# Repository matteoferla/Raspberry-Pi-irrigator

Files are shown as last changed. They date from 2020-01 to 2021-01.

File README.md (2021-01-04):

# Raspberry-Pi-irrigator

> :skull: This project has been superceded by [https://github.com/matteoferla/Somewhat-Smart-Home](https://github.com/matteoferla/Somewhat-Smart-Home).

A Raspberry Pi controlled irrigation system to water plants based on soil moisture.
A pump waters the plant (a peter pepper chilli plant) based on its soil moisture, while the pi camera takes photos of it. 
—last year's attempt at gardening was an unmitigated disaster, so this year I am automating it.

[irrigator.matteoferla.com/](http://irrigator.matteoferla.com/)

This project is ongoing and these are my notes...

## Features

What the schematic looks like...

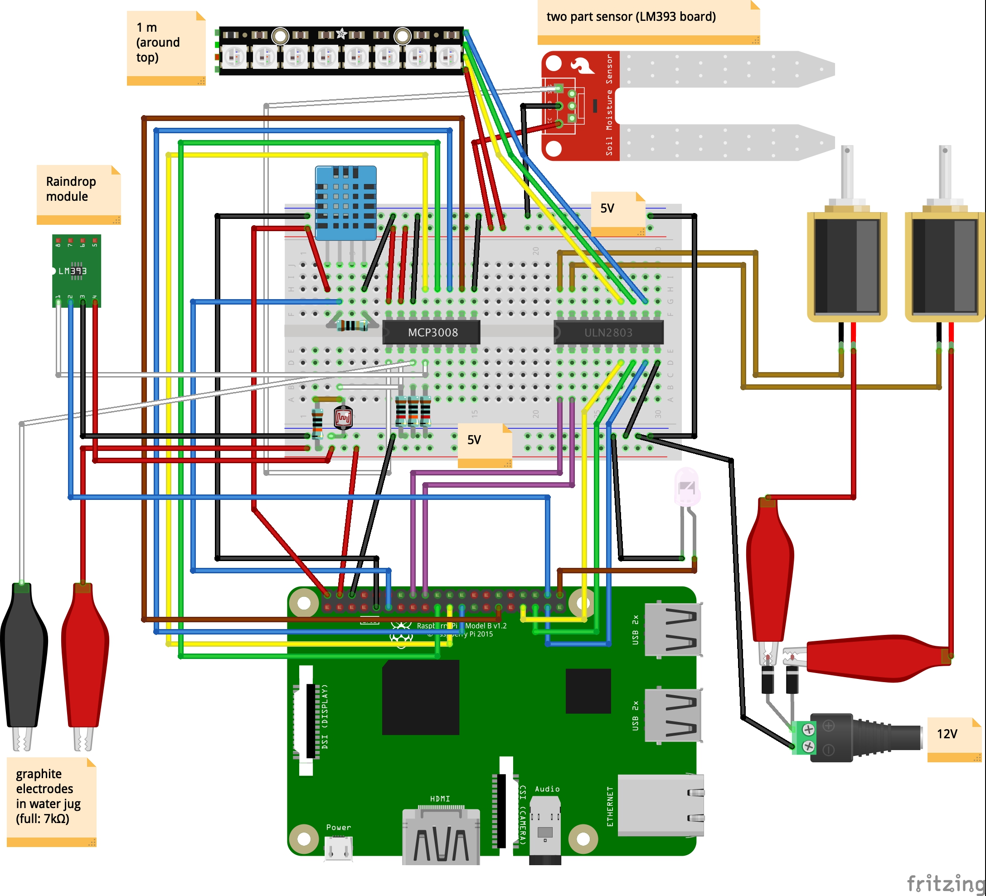
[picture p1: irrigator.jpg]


What it looks like in RL...



### Peter pepper plant

This bad boi is the key component. It's a peter pepper plant.

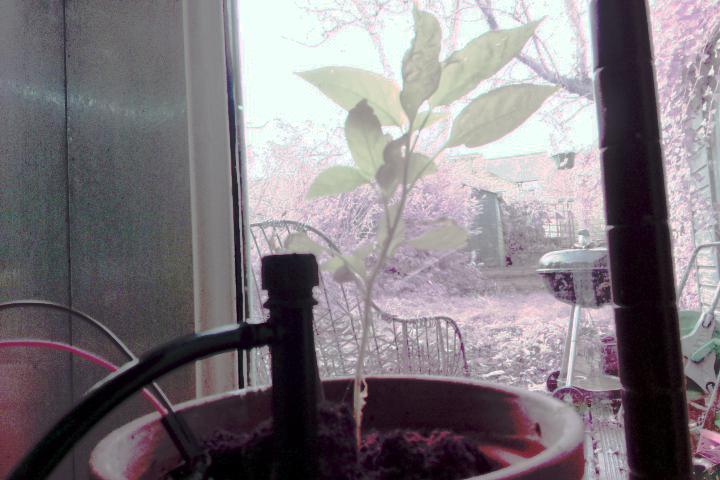
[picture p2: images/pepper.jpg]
pepper


### Pi

I am using a Pi 3+ with a MCP3008 chip and not an Arduino Uno*, because of the website business to check the status.

&lowast;)In my case, a fake Uno by Elegoo. 

I was going to use the Pi Zero but I want to use the camera (wich is for reg pi).

The downside is that my available Pi 3+ has a shorted 3.3V rail.
The reason for the short is that I placed another one the wrong way round —the AMS1117-3.3V voltage regulator on the power module blew a hole!
Maybe one day I will solder in a new PMIC. But for now I am using a externally powering the 5V and 3.3V rails via a breadboard power module MB102.
The GPIO pins and the 3.3V rail measure 2.2V without the external power, but seem fine with.
Powering a pi via the GPIO is bad as it may short the PMIC, due to current spikes.

I am not sure what the actual current is on the 5V and 3.3V rail.
The 12V supply is 2.5A and the module produces a max of 700mA. I'll assume it is that.



A problem with the power for the pi there is a USB and a 12V for the rail and a 12V for the motors and lights...



## pi Camera NoIR

My camera is the infrared camera for night mode.
So what about daytime? Maths to the rescue! (see [camera.md](camera.md))

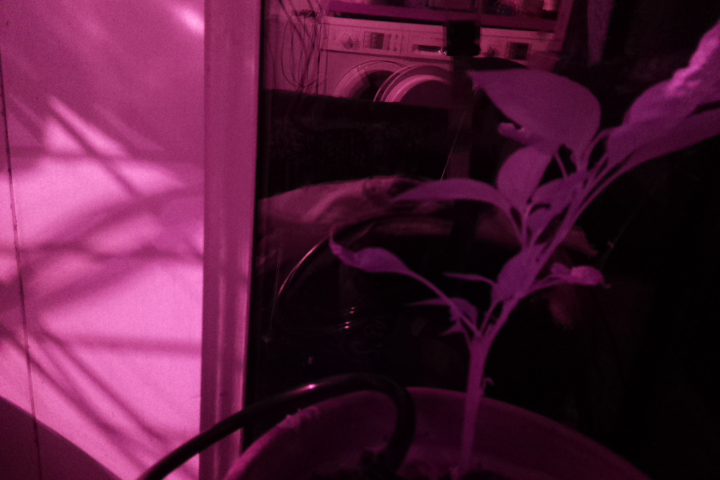
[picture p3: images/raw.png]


After histogram stretching and whitebalance correction in the YCbCr domain:

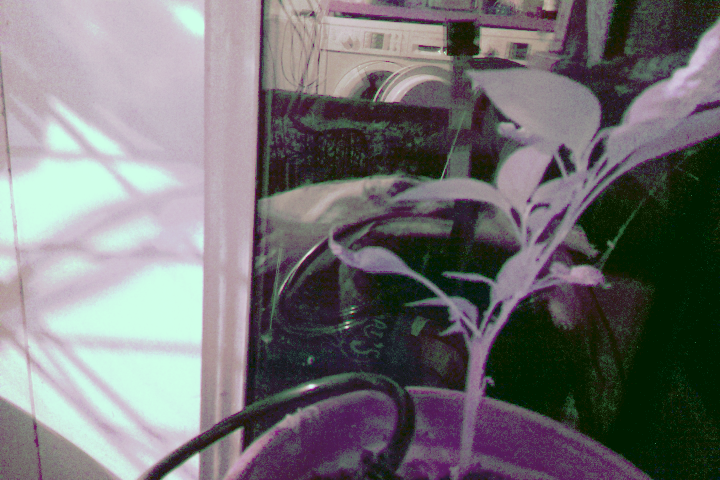
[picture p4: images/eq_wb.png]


For the nighttime, I am using a 1 meter LED strip.

## Photoresistor

Previously, I had the photoresistor in parallel going to ground.
However, this meant that it is was draining too power from the circuit during the day.
As a result, it is now in series with no pulldown.
Current does not flow through the analog in pins of the MCP3008 when it is not reading —hurray.
The GL5528 photoresistors are 10k&Omega; in the dark and 1M&Omega; in the light.
With a 1M&Omega; resistor beforehand in series, 
the output is 2.17V for 10k&Omega; (bright) and 1.7V for 1M&Omega; (dark).

### Formerly: Moisture via YL69
A resistance sensor (YL69 moisture sensor) measures the soil humidity every hour and if the soil resistance goes too low the pump is activated.

The arbitrary value of 50% threshold is based on plying with ramekins with soil. I baked some soil in the oven and then measured different levels of hydration.

I got ages back the YL69 moisture sensor from Kuman kit from Amazon. The YL-69 consists of an electrode and an amplifier (LM393) module. The YL69 oxidises over time (a month apparently).
So further down the line, I will need to switch the electrode to a pair of graphite leads or a capacitance sensor. LM393 is a comparator not a op-amp like a LM358.

Due to the amplifier it is always on.

As promised by the web it did get corroded.



### Moisture via capacitative sensor

I have the analog models. They have in the top part a `TLC555I LinCMOS Timer`, not an op amp or comparator like the others.
No idea what this does exactly.
It draws current even when the analog out is off.

Oddly, the two don't have matching values and aren't that great.

### Water level

The water in the jug is measured by two graphite electrodes. Aka. 2mm graphite cores for mechanical pencils from [Amazon](https://www.amazon.co.uk/gp/product/B0051OCJZ4/).
The jug is a credit card width (8 cm) and tap water has a resistance of 1 k&Omega; so that is 7k&Omega;, when full.
When empty it should be zero —see pulldown problem.



Oddly, the graphite rods had white lettering, which dissolved away leaving flakes.



In two weeks of submersion, the graphite seems fine.

## Pulldown resistors
Pull-down resistors make faint current go to zero. But they also close the circuit!
I put some in at first then took them out as they weren't doing much.

## Temperature

Whereas the DHT11 works fine with the circuitpython `adafruit_dht` library, DHT22 seems to work only with the older `adarfruit_DHT` one.
Here I am using a DHT22.

## Pumps

To water I need pumps and stuff:

* 2x Goso AB11 solenoid pumps [from eBay](https://www.ebay.co.uk/itm/12V-Dosing-Pump-Peristaltic-Head-For-Aquarium-Lab-Analytical-Water-Arduino-DIY/202050095537) in green and blue. The pumps run at 12V 7.5W. SO 7.5W÷12V=0.625A.
* STM ULN2803A Darlington Driver [from eBay](https://www.ebay.co.uk/itm/ULN2803A-Darlington-Driver-TRANSISTOR-ARRAY-8-NPN-x-2-pcs/222622920820). The darlington driver has inbuilt rectifier diodes. 
* AC/DC adaptor 12V⎓3A with standard ⊖-C*-⊕ coaxial and screw jack-thinggy adaptor.



Lessons learnt:

* So the pump out tube needs to be higher ground that the plant or else it flows back and drips.
* Tubing is expensive, but worth it! My cheap black tubing is horrendous: I should have gone for a pricier roll.
 
## Code

I am reusing chunks of code from my previous projects:

* [temp monitor site](https://github.com/matteoferla/Temperature-moniting-website-via-Rasberry-Pi)
* [Spirometry via photoresistor](https://github.com/matteoferla/Spirometry_via_photoresistor)

## Notes

* I connected the two gnds. Not sure if it's a good idea or not.
* Like always during construction I tested chunks of code on the Raspberry via a jupyter notebook it serves across the network (`jupyter notebook --ip="*"`).

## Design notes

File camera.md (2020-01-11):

This what the image looks like in low halogen bulb light 
raw

When I run

    with PiCamera() as camera:
        stream = BytesIO()
        camera.start_preview()
        time.sleep(5)
        camera.capture(stream, format='jpeg')
        stream.seek(0)
        im = Image.open(stream)
        display(im)

So first I apply histrogram stretching.
From [SO](https://stackoverflow.com/questions/7116113/normalize-histogram-brightness-and-contrast-of-a-set-of-images-using-python-im)
I copied the following, which acts on a image.

    def histogram_stretch(im: Image) -> Image:
        h = im.convert("L").histogram()
        lut = []
        for b in range(0, len(h), 256):
            # step size
            step = functools.reduce(operator.add, h[b:b + 256]) / 255
            # create equalization lookup table
            n = 0
            for i in range(256):
                lut.append(n / step)
                n = n + h[i + b]
        # map image through lookup table
        return im.point(lut * 3)
    
While from [here](https://opencv-python-tutroals.readthedocs.io/en/latest/py_tutorials/py_imgproc/py_histograms/py_histogram_equalization/py_histogram_equalization.html)
I made the following, which acts on numpy arrays.

    def histogram_stretch(t: np.ndarray) -> np.ndarray:
        hist,bins = np.histogram(t.flatten(),256,[0,256])
        cdf = hist.cumsum()
        cdf_normalized = cdf * hist.max()/ cdf.max()
        cdf_m = np.ma.masked_equal(cdf,0)
        cdf_m = (cdf_m - cdf_m.min())*255/(cdf_m.max()-cdf_m.min())
        cdf = np.ma.filled(cdf_m,0)
        return cdf[t.astype('uint8')].astype('uint8')

So when I use the pillow Image based histogram_stretch I get:

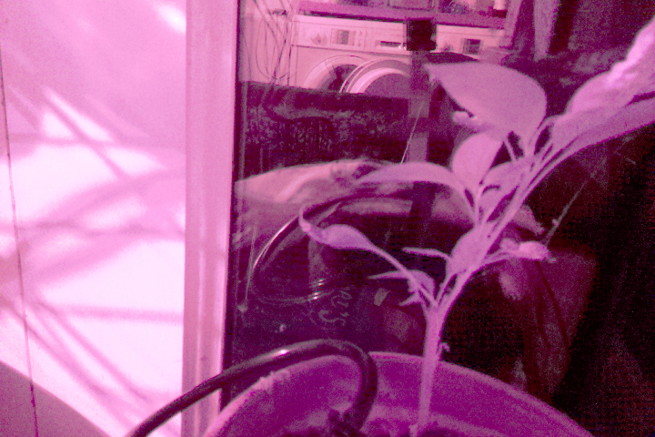
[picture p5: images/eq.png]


From [here](https://codeandlife.com/2019/08/17/correcting-image-white-balance-with-python-pil-and-numpy/)
I copied a white-balance correcting method. It in turn is derived from [SO](https://stackoverflow.com/a/34913974/2721685).
It coverts RGB to the YCbCr domain and centers that —the result is better than centering the three channels (not tested myself):

    def whitebalance(im: Image) -> Image:
        data = np.asarray(im)
        # Convert data and sample to YCbCr
        ycbcr = rgb2ycbcr(data)
        # ysub = rgb2ycbcr(sub)
        # Calculate mean components
        yc = list(np.mean(ycbcr[:, :, i]) for i in range(3))
        # Center cb and cr components of image based on sample
        for i in range(1, 3):
            ycbcr[:, :, i] = np.clip(ycbcr[:, :, i] + (128 - yc[i]), 0, 255)
        rgb = ycbcr2rgb(ycbcr)  # Convert back
        return Image.fromarray(rgb)
        
    def rgb2ycbcr(im: np.ndarray) -> np.ndarray:
        xform = np.array([[.299, .587, .114], [-.1687, -.3313, .5], [.5, -.4187, -.0813]])
        ycbcr = im.dot(xform.T)
        ycbcr[:, :, [1, 2]] += 128
        return ycbcr  # np.uint8(ycbcr)
    
    def ycbcr2rgb(im: np.ndarray) -> np.ndarray
        xform = np.array([[1, 0, 1.402], [1, -0.34414, -.71414], [1, 1.772, 0]])
        rgb = im.astype(np.float)
        rgb[:, :, [1, 2]] -= 128
        rgb = rgb.dot(xform.T)
        np.putmask(rgb, rgb > 255, 255)
        np.putmask(rgb, rgb < 0, 0)
        return np.uint8(rgb)

When I use this on the image equalized by histogram stretching one gets:



This is pretty decent. However, I wonder if I can do better.
In low light in particular, the red channel will saturate before the others,

So I tried histrogram stretching per channel

    def per_channel(t, fx):
        a = [fx(t[:,:,c]) for c in range(3)] #single_channel_gamma
        return Image.fromarray(np.stack(a, axis=-1))
    
    with PiCamera() as camera:
        stream = BytesIO()
        camera.start_preview()
        time.sleep(5)
        camera.capture(stream, format='jpeg')
        stream.seek(0)
        im = Image.open(stream)
        display(im)
        a = np.asarray(im)
        im = per_channel(a, histogram_stretch)
        display(im)
        im = whitebalance(im)
        display(im)

The per channel stretching is actually really good.

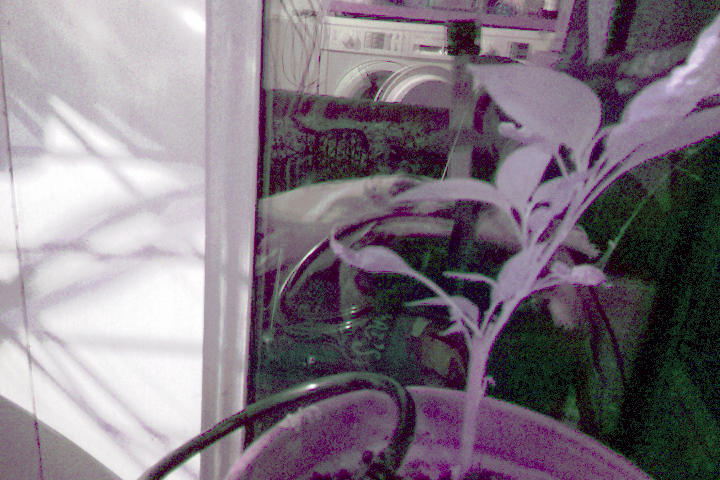
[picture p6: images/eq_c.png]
channel


The whitebalancing in the YCbCr domain does little.

I tried gamma correction per channel, but got mixed results —great during the day, whitewashed at night.

    def single_channel_gamma(matrix: np.ndarray, c=-1, interval=(0,255)) -> np.ndarray:
        minima = np.min(matrix)
        maxima = np.max(matrix)
        scaled = interval[0]+(matrix - minima)/(maxima - minima)*interval[1]
        median = np.median(scaled)
        gamma = np.log((interval[1]-interval[0])/2)/np.log(median)
        #print(['Grey', 'Red', 'Green', 'Blue','Alpha'][c+1],'median', median,'gamma', gamma)
        gc = np.power(scaled,gamma)
        np.putmask(gc, gc > interval[1], interval[1])
        np.putmask(gc, gc < interval[0], interval[0])
        return gc

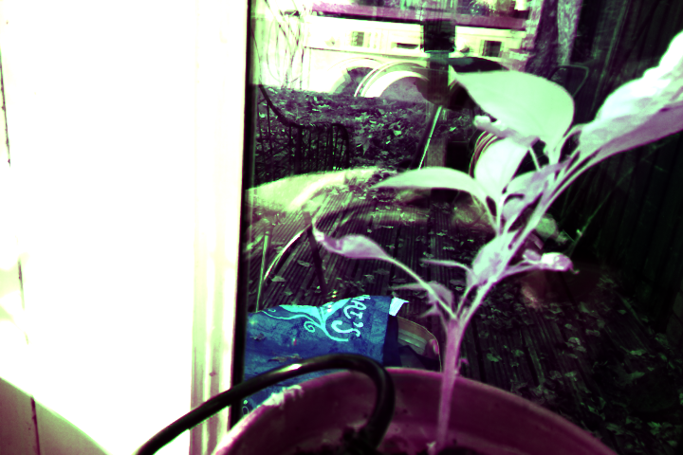
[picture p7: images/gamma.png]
gamma


CV2 CLAHE (per channel) fails so I gave up quickly. I tried one or two things more and go great images like this:

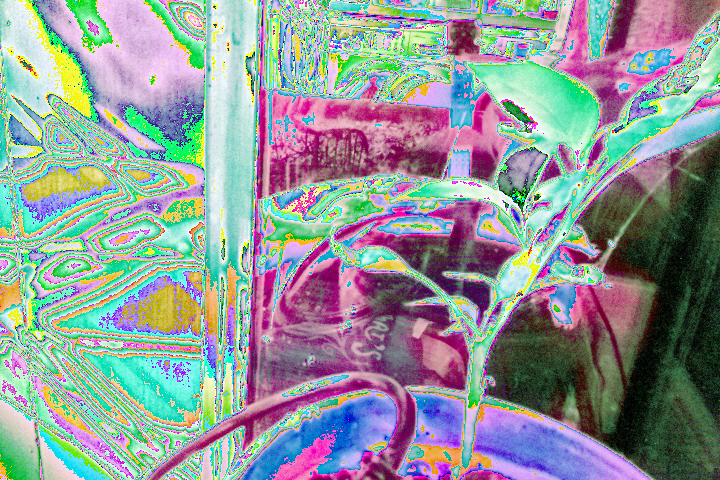
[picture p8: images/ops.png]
ops


One thing is the granularity.
Changing the shutter speed will not solve the problem that
the red channel is a lot higher than the others.
Therefore I took 100 photos and summed the arrays together.

    def per_channel(t, fx):
        a = [fx(t[:,:,c]) for c in range(3)] #single_channel_gamma
        return Image.fromarray(np.stack(a, axis=-1))
    
    def scale(matrix: np.ndarray, interval=(0,255)) -> np.ndarray:
        minima = np.min(matrix)
        maxima = np.max(matrix)
        scaled = (matrix - minima)/(maxima - minima)*interval[1] + interval[0]
        return scaled
    
    def histogram_stretch(t: np.ndarray) -> np.ndarray: 
        hist,bins = np.histogram(t.flatten(),256,[0,256])
        cdf = hist.cumsum()
        cdf_normalized = cdf * hist.max()/ cdf.max()
        cdf_m = np.ma.masked_equal(cdf,0)
        cdf_m = (cdf_m - cdf_m.min())*255/(cdf_m.max()-cdf_m.min())
        cdf = np.ma.filled(cdf_m,0)
        return cdf[t.astype('uint8')].astype('uint8')
    
    with PiCamera() as camera:
        stream = BytesIO()
        camera.start_preview()
        time.sleep(5)
        stacked = np.zeros((480, 720, 3))
        for i in range(100):
            stream = BytesIO()
            camera.capture(stream, format='jpeg')
            stream.seek(0)
            im = Image.open(stream)
            #stacked = np.add(stacked, histogram_stretch(np.asarray(im)))
            stacked = np.add(stacked, np.asarray(im))
        fx = lambda m: histogram_stretch(scale(m))
        im = per_channel(stacked, fx)
        display(im)

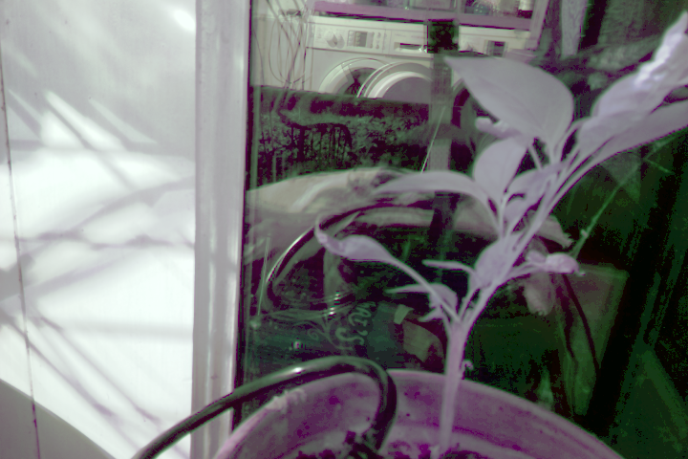
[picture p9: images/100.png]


This killed the granularity but not the weird color.

However, this challenge is interesting, but is a bit silly: an LED will fix the issue.

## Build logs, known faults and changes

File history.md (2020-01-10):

passwd
git clone https://github.com/matteoferla/Raspberry-Pi-irrigator.git irrigator
wget https://github.com/jjhelmus/berryconda/releases/download/v2.0.0/Berryconda3-2.0.0-Linux-armv7l.sh
bash Berryconda3-2.0.0-Linux-armv7l.sh
rm Berryconda3-2.0.0-Linux-armv7l.sh
exit

conda update --all
conda install -y scipy
conda install -y opencv
conda install -y jupyter
sudo apt-get install libgpiod2
cd irrigator
which pip
pip install -r requirements.txt 
sudo raspi-config # camera and spi
sudo shutdown -r now

cd irrigator
# trialling...
python app.py
# then...
nohup /home/pi/berryconda3/bin/python app.py &
# eventually...
sudo cp irrigator.service /etc/systemd/system/irrigator.service
sudo systemctl start irrigator.service
sudo systemctl enable irrigator.service

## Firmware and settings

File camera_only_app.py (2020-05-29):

from core import app  # Flask app is initiated but without Models
from models import db, Measurement  # Models initiated.
from scheduled import Schedule

from waitress import serve
import os, json
from flask import render_template, request, Response
from datetime import datetime, timedelta, time


############ View

def read_data(start, stop):
    dt = []
    temp = []
    hum = []
    b = []
    wtA = []
    wtB = []
    moistA = []
    moistB = []
    for m in Measurement.query.filter(Measurement.datetime > start) \
            .filter(Measurement.datetime < stop).all():  # Measurement.query.all():
        temp.append(m.temperature)
        dt.append(m.datetime)
        hum.append(m.humidity)
        b.append(m.brightness)
        wtA.append(m.wateringtime_A)
        moistA.append(m.soil_A_moisture)
        wtB.append(m.wateringtime_B)
        moistB.append(m.soil_B_moisture)
    # smooth = lambda a: savgol_filter(a, 31, 3).tolist()
    smooth = lambda a: a
    return dict(datetime=json.dumps([d.strftime('%Y-%m-%d %H:%M:%S') for d in dt]),
                temperature=smooth(temp),
                humidity=smooth(hum),
                soil_A_moisture=smooth(moistA),
                soil_B_moisture=smooth(moistB),
                brightness=smooth(b),
                wateringtime_A=smooth(wtA),
                wateringtime_B=smooth(wtB))

@app.route('/')
def serve_data():
    if 'stop' in request.args:
        # %Y-%m-%d
        stop = datetime(*map(int, request.args.get('stop').split('-')))
    else:
        stop = datetime.now()
    if 'start' in request.args:
        start = datetime(*map(int, request.args.get('start').split('-')))
    else:
        start = datetime.combine((datetime.now() - timedelta(days=5)).date(), time.min)
    data = read_data(start, stop)
    return render_template('moisture.html',
                           today=str(datetime.now().date()),
                           yesterday=str((datetime.now() - timedelta(days=1)).date()),
                           threedaysago=str((datetime.now() - timedelta(days=3)).date()),
                           aweekago=str((datetime.now() - timedelta(days=7)).date()),
                           #watertimetext_A=[str(x) + ' sec.' for x in data['wateringtime_A']],
                           #watertimetext_B=[str(x) + ' sec.' for x in data['wateringtime_B']],
                           N_elements=len(data['datetime']),
                           album=list(sorted(os.listdir('static/plant_photos'), reverse=True))[:24:3],
                           **data)

@app.route('/trigger')
def sense_route():
    if 'mode' in request.args:
        mode = request.args.get('mode')
    else:
        mode = 'all'
    if 'key' not in request.args:
        return Response(status=401)
    elif request.args.get('key') != os.environ['IRRIGATOR_KEY']:
        return Response(status=401)
    if mode == 'all':
        # schedule.check_tank()
        # schedule.check_spill()
        # schedule.sense()
        schedule.photo()
    elif mode == 'photo':
        schedule.photo()
    elif mode == 'measure':
        return 'DISABLED'
    elif mode == 'tank':
        return 'DISABLED'
    elif mode == 'water':
        return 'DISABLED'
    else:
        pass
    return 'OK'


############# Main
if __name__ == '__main__':
    schedule = Schedule(sense=False, photo=True, spill=False, bright=False)
    if not os.path.exists('moisture.sqlite'):
        db.create_all()
    serve(app, host='0.0.0.0', port=5000)

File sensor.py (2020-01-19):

#MCP3008 modules
import adafruit_mcp3xxx.mcp3008 as MCP
from adafruit_mcp3xxx.analog_in import AnalogIn
#import adafruit_dht
import Adafruit_DHT
import busio
import digitalio
import board
import time
from picamera import PiCamera
from PIL import Image
from io import BytesIO
import numpy as np
from datetime import datetime
import os
import RPi.GPIO as GPIO
from collections import namedtuple

### startup ###############################################################
if not os.path.exists('static'):
    os.mkdir('static')
if not os.path.exists('static/plant_photos'):
    os.mkdir('static/plant_photos')

spi = busio.SPI(clock=11, MISO=9, MOSI=10)
cs = digitalio.DigitalInOut(board.D5)
mcp = MCP.MCP3008(spi, cs)

## classes  ###############################################################

class Pins:
    """
   * DHT11 is connected to GPIO17 and powered by 3.3V without a pull resistor (DHT22 sensor not working)
    * MCP3008 is D_out -> MISO: GPIO9, D_in -> MOSI:GPIO10, Clock: GPIO11 and CS GPIO05
    * Pumps are connected to GPIO23 and GPIO24 (the two pins between two GND)
    """

    mcp = mcp
    pumps = (digitalio.DigitalInOut(board.D23), digitalio.DigitalInOut(board.D24))
    pumps[0].direction = digitalio.Direction.OUTPUT
    pumps[1].direction = digitalio.Direction.OUTPUT
    spill = digitalio.DigitalInOut(board.D20)
    spill.direction = digitalio.Direction.INPUT
    soil_limits = [1.2, 3.2]

    @property
    def dht(self):
        # imitating the circuitpython dht
        fauxDHT = namedtuple('DHT', ['humidity', 'temperature'])
        return fauxDHT(*Adafruit_DHT.read(22, 17))

    @property
    def brightness(self):
        """
        Corrected to percent based on the values outputted by using 10k&Omega; and 1M&Omega; resistors.
        :return: brightness
        """
        return round((AnalogIn(mcp, MCP.P0).voltage -1.7)/(2.2-1.7)*100)

    @property
    def temperature(self):
        for i in range(10):
            t = self.dht.temperature
            if t is not None:
                return t
        else:
            raise ValueError('Cannot read temperature')

    @property
    def humidity(self):
        for i in range(10):
            h = self.dht.humidity
            if h is not None:
                return h
        else:
            raise ValueError('Cannot read humidity')

    def get_soil_moisture(self, number):
        pin = [MCP.P3, MCP.P4][number]
        return round(100 - (AnalogIn(self.mcp, pin).voltage - self.soil_limits[0]) / (self.soil_limits[1] - self.soil_limits[0]) * 100)

    @property
    def soil_B_moisture(self):
        return self.get_soil_moisture(1)

    @property
    def soil_A_moisture(self):
        return self.get_soil_moisture(0)

    def engage_pump(self, number=0, secs=1):
        self.pumps[number].value = True
        time.sleep(secs)
        self.pumps[number].value = False
        return self


    @property
    def tank_filled(self):
        if self.tank_level > 1.5:
            return True
        else:
            return False

    @property
    def tank_level(self):
        return AnalogIn(self.mcp, MCP.P1).voltage

    @property
    def spill_analog(self):
        return AnalogIn(self.mcp, MCP.P2).voltage

    @property
    def spilled(self):
        # Three pronged: error, D0 and A0
        # just in case.
        try:
            if not self.spill.value:
                return 'Spill detected by the digital pin'
            elif self.spill_analog < 2:
                return 'Spill detected by the analogue pin '+self.spill_analog
            else:
                return None
        except Exception as err:
            return f'Possible spill caused by a shortcircuit ({err})'


    def cleanup(self):
        GPIO.cleanup()

###################################################

class Flash:
    light = digitalio.DigitalInOut(board.D21)
    light.direction = digitalio.Direction.OUTPUT
    strip = (digitalio.DigitalInOut(board.D13), #R
             digitalio.DigitalInOut(board.D19), #G
             digitalio.DigitalInOut(board.D26)) #B
    for i in range(3):
        strip[i].direction = digitalio.Direction.OUTPUT

    def __init__(self, mode='strip'):
        self.mode = mode
        assert mode in ('led', 'strip')

    def __enter__(self):
        if self.mode == 'strip':
            for i in range(3): self.strip[i].value = True
        else:
            self.light = True
        return self

    def __exit__(self, exc_type, exc_val, exc_tb):
        self.light = False
        for i in range(3): self.strip[i].value = False

###################################################

class Photo:
    _camera = None
    # see also a SIGINT death safeguard.
    # it is this or the gc ...

    def __init__(self, warmup=5, mode='strip'):
        self.data = np.zeros((480, 720, 3))
        with PiCamera() as self.camera:
            self.__class__._camera = self.camera # death prevention..
            self.camera.start_preview()
            time.sleep(warmup)
            with Flash(mode=mode):
                while np.max(self.data) < 255:
                    self.data = np.add(self.data, np.asarray(self.capture()))
        self.__class__._camera = None
        self.data = self.per_channel(self.scale, self.data)
        self.data = self.per_channel(self.histogram_stretch, self.data)
        self.image = Image.fromarray(self.data)
        self.save()

    @staticmethod
    def per_channel(fx, t):
        a = [fx(t[:, :, c]) for c in range(3)]
        return np.stack(a, axis=-1)

    @staticmethod
    def scale(matrix: np.ndarray, interval=(0, 255)) -> np.ndarray:
        minima = np.min(matrix)
        maxima = np.max(matrix)
        scaled = (matrix - minima) / (maxima - minima) * interval[1] + interval[0]
        return scaled

    @staticmethod
    def histogram_stretch(t: np.ndarray) -> np.ndarray:
        hist, bins = np.histogram(t.flatten(), 256, [0, 256])
        cdf = hist.cumsum()
        cdf_normalized = cdf * hist.max() / cdf.max()
        cdf_m = np.ma.masked_equal(cdf, 0)
        cdf_m = (cdf_m - cdf_m.min()) * 255 / (cdf_m.max() - cdf_m.min())
        cdf = np.ma.filled(cdf_m, 0)
        return cdf[t.astype('uint8')].astype('uint8')

    def capture(self) -> Image:
        stream = BytesIO()
        self.camera.capture(stream, format='jpeg')
        stream.seek(0)
        im = Image.open(stream)
        return im

    def rotate(self) -> Image:
        # Image
        return self.image.transpose(Image.ROTATE_180)

    def save(self):
        self.image.save('static/plant_photos/'+datetime.now().isoformat(timespec='seconds')+'.jpg')

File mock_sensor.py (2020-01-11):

__doc__ = """This is just a mock sensor to test the code in PyCharm on my Macbook,
while the real sensor class is tested in a Jupyter notebook hosted on the pi.
"""

import random
from PIL import Image

class MockPins:

    @property
    def moisture(self):
        return random.randint(0, 100)

    @property
    def brightness(self):
        return random.randint(0, 100)

    @property
    def temperature(self):
        return random.randint(20, 30)

    @property
    def humidity(self):
        return random.randint(0, 100)

    def engage_pump(self, number=0, secs=1):
        return self

class Photo:
    pass

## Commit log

2020-01-04 :art: diagram
    [irrigator.fzz]
2020-01-04 :zap: improved circuit
    [irrigator.fzz]
2020-01-05 :art: image had mistake
    [irrigator.fzz]
2020-01-06 :art: image had no 10kOhm pulldown
    [irrigator.fzz]
2020-01-06 :hammer: calibrated soil
2020-01-07 :beetle: all fixed up
    [app.py]
2020-01-08 :chain: link to site
2020-01-09 :camera: take photos!
2020-01-09 :beetle: path was wrong
    [sensor.py]
2020-01-09 :beetle: os.listdir in wrong folder
    [app.py]
2020-01-09 :camera: the image is not 180deg thank to zipties...
2020-01-11 :pencil: documenting camera
2020-01-11 :camera: changes
2020-01-12 :constructions: upgrades
    [irrigator.fzz]
2020-01-12 :construction: defaulting to led strip
2020-01-13 :beetle: camera issues
2020-01-13 :beetle: any change takes too long...
    [app.py, sensor.py]
2020-01-13 :beetle: add prints to debug
2020-01-13 :beetle: Issue was DHT stopped working.
    [app.py]
2020-01-14 :beetle: cables keep unplugging!
2020-01-18 :beetle: faux sensor failed
    [sensor.py]
2020-01-31 :hammer: more data points for brightness
    [irrigator.fzz]
2020-05-29 :hammer: split stuff up so can run without sensors
